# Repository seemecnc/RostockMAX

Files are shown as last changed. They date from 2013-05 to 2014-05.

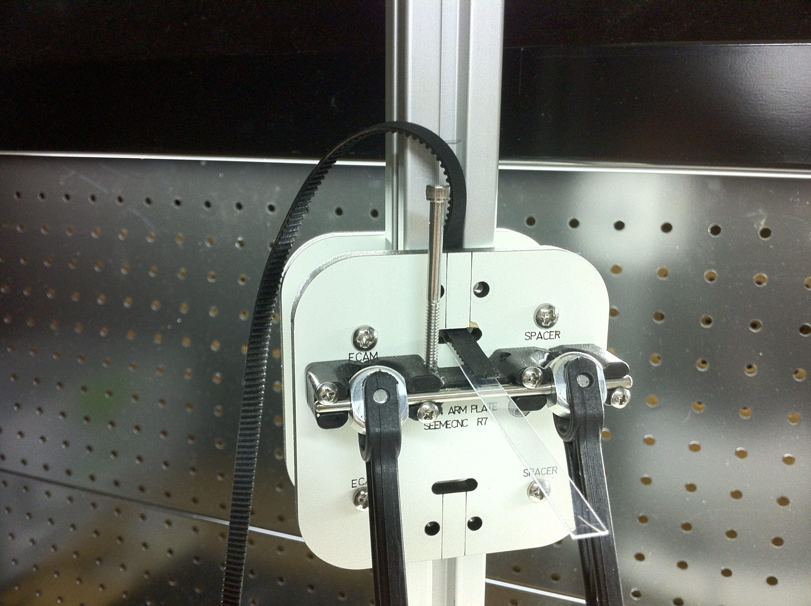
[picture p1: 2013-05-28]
ASSEMBLY_MANUAL/belt-routing-trick.jpg

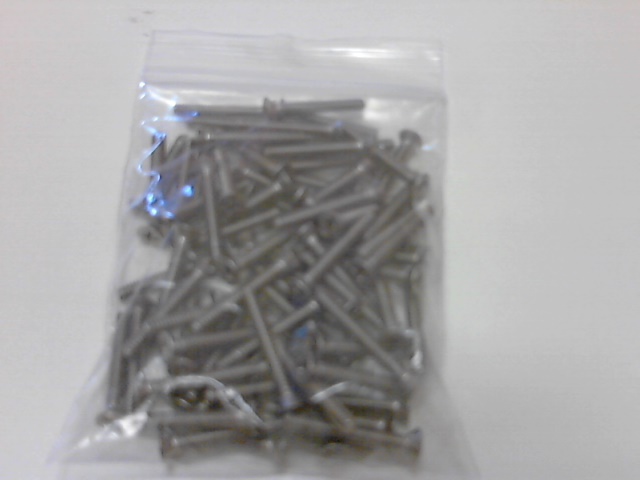
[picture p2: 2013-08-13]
PACKING_LIST/img/Picture 91.jpg

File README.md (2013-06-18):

RostockMAX
==========
Author:  SeeMeCNC
Initially created here on github 5/28/2013, origionally hosted on reprap.org
Source files for the Rostock MAX Delta 3D Printer by SeeMeCNC

Use the CAD_FILES folder to obtain the source cad files such as the dxf's for lasercut parts, .stl and .iges 
files for other parts.   

For the assembly manual, use the folder ASSEMBLY_MANUAL

Note that github has problems with large files.  If you get the error, "Error: blob is too big" when
trying to view the PDF file, you can obtain it here: 
http://www.geneb.org/rostock-max/Rostock-MAX-Assembly-Guide.pdf

For firmware, use the repo http://github.com/seemecnc/RepetierMAX

For the new EZStruder, which started shipping with all kits around 5/20/13, please see
https://github.com/seemecnc/EZStruder

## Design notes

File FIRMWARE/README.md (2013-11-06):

# Repetier-Firmware - the fast and user friendly firmware

##########  Modified by SeeMeCNC for use with the Rostock MAX kits ###########
This firmware has changes made specific to the Rostock MAX.  Mainly, calibartion settings etc... as well as
some functionalities for the RAMBo board by ultimachine.

PLEASE CHECK THE CONFIGURATION.H FILE BEFORE UPLOADING
Check the steps per mm settings, pulley tooth count etc... to make sure they correspond with 
your machine's settings

For questions regarding changes, email johnoly (john@seemecnc.com)

by repetier  (repetierdev@gmail.com)

For documentation please visit [http://www.repetier.com/documentation/repetier-firmware/](http://www.repetier.com/documentation/repetier-firmware/)

Beta version with added delta move and homing calculations and several other features for delta printers.

To set rod height on a delta printer use command M251 which will allow you to measure 
the rod length or, if you have an LCD panel then you can select delta calibration in the
configuration menu.

Version 0.81  03.02.2013

## Introduction

Repetier-Firmware is a firmware for RepRap like 3d-printer powered with
an arduino compatible controller.
This firmware is a nearly complete rewrite of the sprinter firmware by kliment
which based on Tonokip RepRap firmware rewrite based off of Hydra-mmm firmware.
Some ideas were also taken from Teacup, Grbl and Marlin.

Supported boards:

The following boards are supported by setting the proper motherboard type.Other boards
require a matching pin definition.

* MEGA/RAMPS up to 1.2       = 3
* RAMPS 1.3/RAMPS 1.4        = 33
* Gen6                       = 5 
* Gen6 deluxe                = 51
* Sanguinololu up to 1.1     = 6
* Sanguinololu 1.2 and above = 62
* Gen7 1.1 till 1.3.x        = 7
* Gen7 1.4.1 and later       = 71
* Teensylu (at90usb)         = 8 // requires Teensyduino
* Printrboard (at90usb)      = 9 // requires Teensyduino
* Foltyn 3D Master           = 12
* MegaTronics                = 70
* RUMBA                      = 80  // Get it from reprapdiscount
* Rambo                      = 301

## Features

- RAMP acceleration support.
- Path planning for higher print speeds.
- Trajectory smoothing for smoother lines.
- Ooze prevention system for faster anti ooze then slicer can do,
- Nozzle pressure control for improved print quality with RAMPS.
- Fast - 40000 Hz and more stepper frequency is possible with a 16 MHz AVR. 
- Multiple extruder supported (max. 6 extruder).
- Standard ASCII and improved binary (Repetier protocol) communication.
- Autodetect the command protocol, so it will work with any host software.
- Continuous monitoring of one temperature.
- Important parameters are stored in EEPROM and can easily be modified without
  recompilation of the firmware.
- Stepper control is handled in an interrupt routine, leaving time for
  filling caches for next move.
- PID control for extruder/heated bed temperature.
- Interrupt based sending buffer (Arduino library normally waits for the
  recipient to receive written data)
- Small RAM memory print, resulting in large caches.
- Supports SD-cards.
- mm and inches can be used for G0/G1
- Arc support
- Works with Skeinforge 41, all unknown commands are ignored.
- Dry run : Execute yout GCode without using the extruder. This way you can
  test for non-extruder related failures without actually printing.

## Controlling firmware

Also you can control the firmware with any reprap compatible host, you will only get
the full benefits with the following products, which have special code for this
firmware:

* [Repetier-Host for Windos/Linux](http://www.repetier.com/download/)
* [Repetier-Host for Mac](http://www.repetier.com/download/)
* [Repetier-Server](http://www.repetier.com/repetier-server-download/)

## Installation

For documentation and installation please visit 
[http://www.repetier.com/documentation/repetier-firmware/](http://www.repetier.com/documentation/repetier-firmware/).

## Changelog

See changelog.txt

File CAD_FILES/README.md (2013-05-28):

RostockMAX CAD source files
==========

Source files for the Rostock MAX Delta 3D Printer by SeeMeCNC
These files are distibuted GPL, feel free to enjoy, but give credit where due.

The DXFs folder contains the 4 lasercut sheets needed to cut the parts for a Rostock MAX.

Sheets 1 thru 3 are 18" x 32" x .270" thick melamine laminate, and the files have been optimized for
that material.  It also works with 1/4" acrylic, however the tabs are slightly oversized for 1/4" material.

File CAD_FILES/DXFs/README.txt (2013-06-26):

Rostock MAX dxf files of laser cut parts

The newest files are WOOD RMAX EZ SHEET x OF 3.dxf

These files are what are shipping as of 6/15, the older SHEETx.dxf files have
the old style side mounted extruder mounts etc...

26Jun13 gwb Added "RMAX EXTRUDER MOUNTING KIT.DXF" - this is just the parts needed to
            make the new top mounted extruder and spool mount.

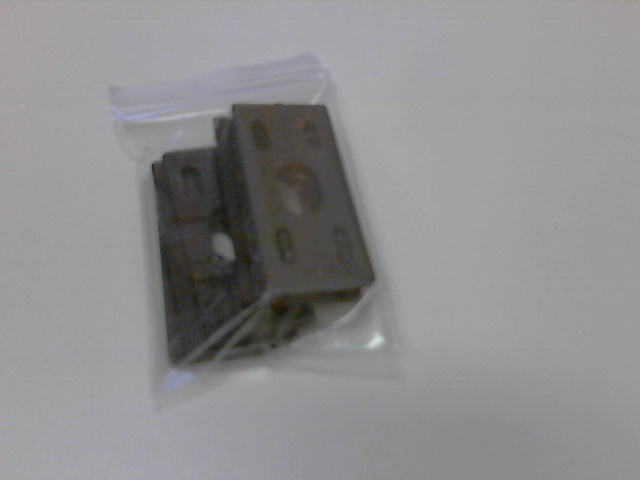
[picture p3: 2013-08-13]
PACKING_LIST/img/Picture 102.jpg

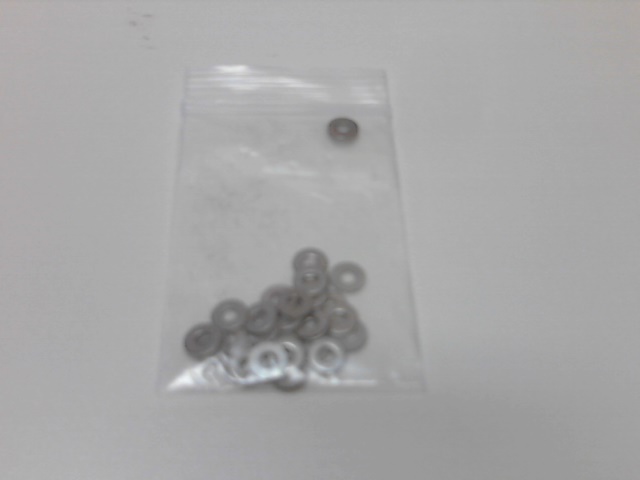
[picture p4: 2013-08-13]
PACKING_LIST/img/Picture 79.jpg

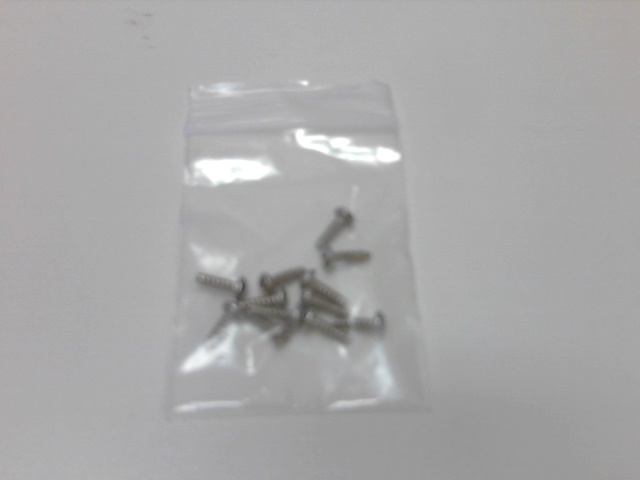
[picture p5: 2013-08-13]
PACKING_LIST/img/Picture 81.jpg

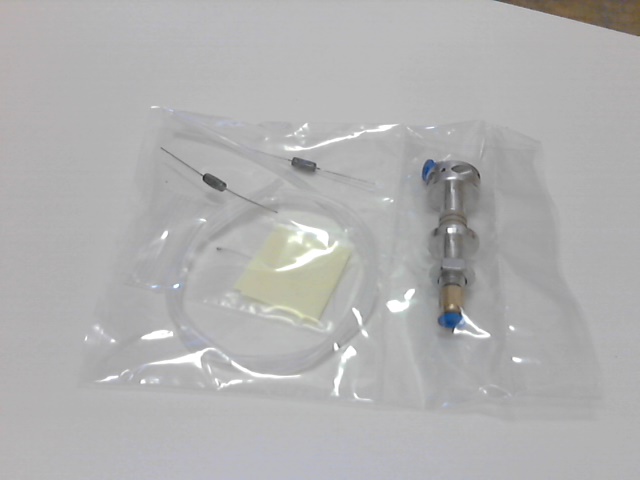
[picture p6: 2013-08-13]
PACKING_LIST/img/Picture 122.jpg

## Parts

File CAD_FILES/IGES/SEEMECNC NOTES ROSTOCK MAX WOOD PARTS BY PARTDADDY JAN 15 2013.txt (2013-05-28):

by PartDaddy
Jan 25, 2013

To our peers in the open source community...

Here's the Rostock MAX IGES files so many of you requested. Yes, I know how hard it is to 
reverse engineer STL files. 

These IGES files should work for just about any CAD software. If they do not,
email us and I will fixt them.

~Steve Wygant aka PartDaddy

SeeMeCNC

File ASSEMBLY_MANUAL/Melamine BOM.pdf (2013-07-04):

Sheet1

Part # | Qty | Description
68324 | 1 Hot End Spacer
68328 | 1 Hot End Adapter
68343 | 3 Carriage Plate
68344 | 3 Arm Plate
68345 | 2 Spool Axle
68351 | 1 Table
68352 | 3 | Tri Support
68355 | 1 Base
68356 | 1 Power Supply Retainer
68357 | 1 Support Panel
68358 | 1 Door
68361 | 7 Cover Bracket
68364 | 3 Motor Mount
68368 | 1 Top Support Plate
68369 | 6 Idler Mount
68370 | 3 Top Clamp
68377 | 3 T Slot Support
68381 | 6 Axle Support
68387 | 2 | Extruder Bracket
68388 | 3 | Spacer Extruder Support
68389 | 1 | Extruder Clamp
68392 | 2 Bracket For Filament Spool
68410 | 1 LCD Face
68411 | 2 Stand Off LCD
70769 | 3 | Spacer (top mounted extruder)
70770 | 1 | Brace (top mounted extruder)
70771 | 1 Part A (Spool holder)
70772 | 1 Part B (Spool holder)
70773 | 2 Arm (Spool holder)
70774 | 1 Part C (Spool holder)
70777 | 1 | Motor Support (top mounted extruder)
70778 | 1 | EZStruder Adapter Hanger
70779 | 1 | EZStruder Adapter
N/A | 2 Door Keeper
Total | 72

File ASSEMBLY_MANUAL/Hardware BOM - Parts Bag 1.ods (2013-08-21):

Part # | Qty | Description
Parts Bag #1
30650 | 6 | 2-56 Pan head screws
30642 | 6 | 2-56 Hex nuts
30006 | 6 | 6-32x5/8” Socket Head Cap Screw
30037 | 22 | 6-32x2” Pan head screws
30034 | 10 | 6-32x1.75” Pan head screw
32005 | 25 | ¼-20 T-Slot Nut
30419 | 25 | ¼-20 Button Head Cap Screw
29998 | 6 | 10x32x5/8” Nylon Pan Head Screw
30170 | 6 | Nylon Hex Nut
44010 | 6 | Rubber Foot
17505 | 6 | Leg for #44010 Rubber Foot
30449 | 26 | #4 Flat Washer
30251 | 12 | #4x1/4” Pan Head Sheet Metal Screw
30250 | 12 | #4x3/8” Pan Head Sheet Metal Screw
30222 | 27 | 4-40 T-Nut
30238 | 4 | 4-40x1-1/4” Pan Head Screw
30236 | 16 | 4-40x3/4” Flat Head Screw
30232 | 12 | 4-40x1/2” Socket Head Cap Screw
30318 | 12 | M3x.5 Pan Head Screw
30121 | 4 | 6-32x1/2” Nylon Pan Head Screw
30450 | 50 | #6 Flat Washer
35065 | 24 | 608ZZ Ball Bearing
30164 | 114 | 6-32 Nylon Lock Nut
30132 | 78 | 6-32x1” Flat Head Screw

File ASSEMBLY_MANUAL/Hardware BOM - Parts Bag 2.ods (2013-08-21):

Part # | Qty | Description
Parts Bag #2
68309 | 12 | Universal Joint
68326 | 18 | Cheapskate Carriage Bearing Spacer
68340 | 18 | Cheapskate Idler Bearing Spacer
68334 | 3 | Hot End Platform Spacer (Aluminum)
63825 | 6 | U-Joint Axles
68315 | 12 | Cheapskate Eccentric Carriage Tensioner

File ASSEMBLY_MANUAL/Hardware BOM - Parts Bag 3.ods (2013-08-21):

Part # | Qty | Description
Parts Bag #3
71505 | 20 | Plastic Spacers
71622 | 6 | Belt Clamps
68332 | 3 | Carriage Base
68304 | 2 | Platform Halves
58761 | 6 | Binder Clips
26159 | 1 | Toggle Switch
26164 | 15 | Wire Ties
39835 | 1 | 20 Tooth GT2 Timing Pulley Kit
 |  | 3 Pulleys, 6 Set Screws, 1 Allen Wrench
68303 | 6 | Rostock MAX Molded Arms

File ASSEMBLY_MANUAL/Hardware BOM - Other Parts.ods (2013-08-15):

Part # | Qty | Description
Onyx Bed Pack
70505 | 6 | Plastic Spacers
30236 | 6 | 4-40x3/4” Flat Head Screw
30222 | 6 | 4-40 T-Nut
 | 1 | 100K Thermistor
 | 1 | Red LED
 | 1 | 4.7K Resistor
58742 | 1 | 300MM Onyx Round Heated Bed
 | 1 | Onyx Laser Cut Insulator
Electronics
 | 1 | RAMBo Electronics Package
 |  | (Incl. Board, end stop wiring and thermistor wires)
26720 | 1 | RRD LCD Controller with SD card and RAMBo
 |  | LCD Adapter
 | 1 | USB Cable
26501 | 4 | NEMA 17 Stepper Motor
26309 | 1 | 25MMx25MMx10MM 12v Fan
 | 1 | ATX Power Supply
Miscellaneous
26602 | 1 | 300MM Borosilicate Glass Build Plate
 |  | Included in kits purchased after 8/11/2013
 | 3 | 32” Aluminum Extrusions
Belt Pack
 | 3 | 75” GT2 2MM Pitch Belts
68336 | 30 | Bearing Covers
Hot End Pack
 | 2 | 6.8 Ohm Heating Resistors
 | 1 | 100k Thermistor
 | 1 | 24”x2MM ID x 4MM OD PTFE Tubing
 | 2 | 4MM PTC Fitting
 | 1 | Assembled Hot End
 | 1 | 2” PTFE sleeve for thermistor wires

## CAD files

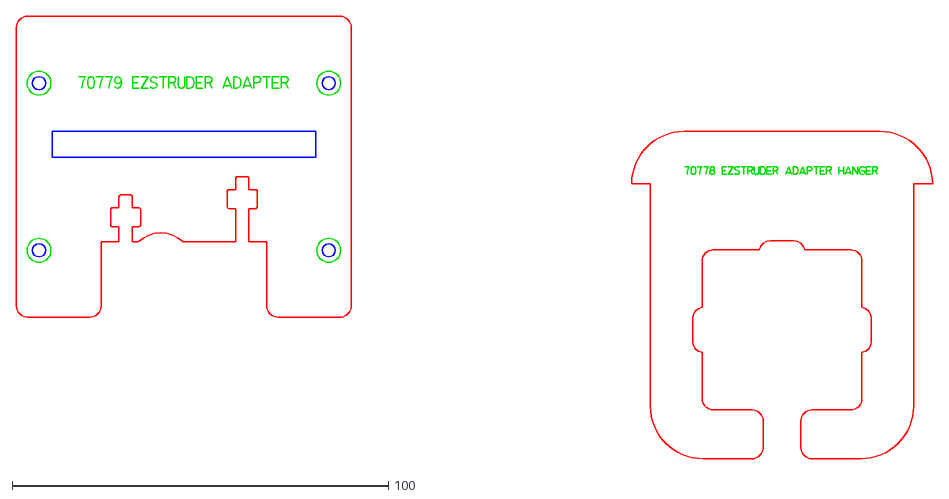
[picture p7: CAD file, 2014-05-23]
CAD_FILES/DXFs/EZSTRUDER_HANGER_ADAPTER.DXF
243.5 x 117.6

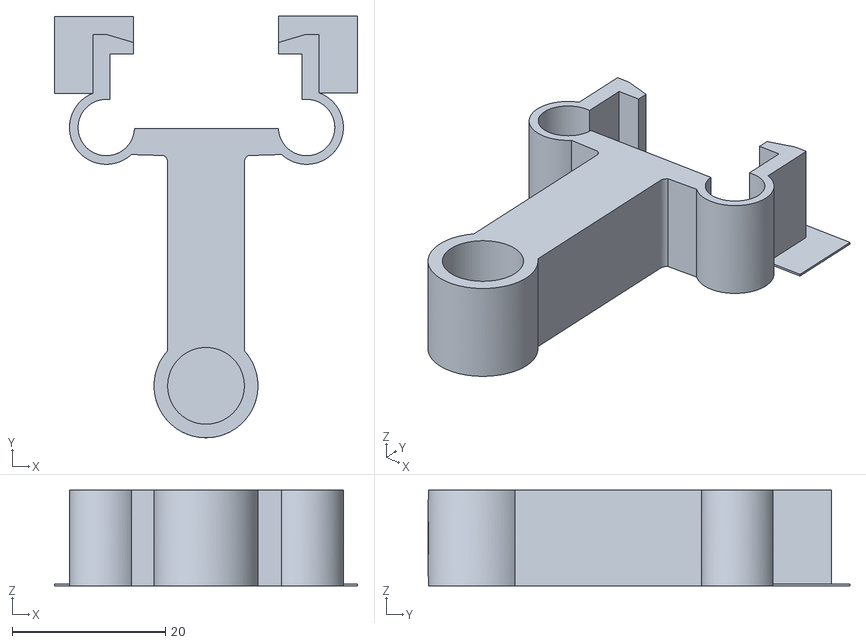
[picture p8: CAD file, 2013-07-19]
PRINTED_ADDONS/wire guide post mounting clip.stl
39.5 x 55.0 x 12.5

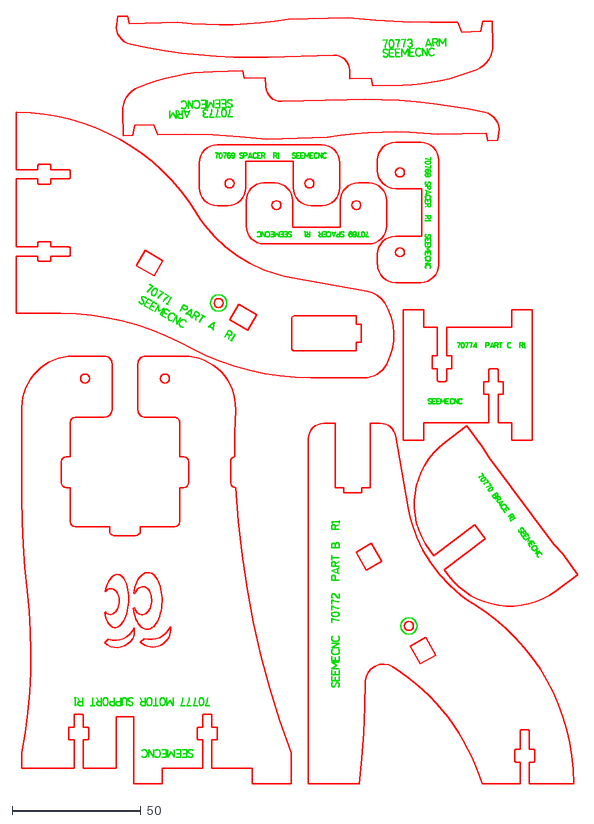
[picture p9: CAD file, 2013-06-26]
CAD_FILES/DXFs/RMAX EXTRUDER MOUNTING KIT.dxf
218.1 x 298.1

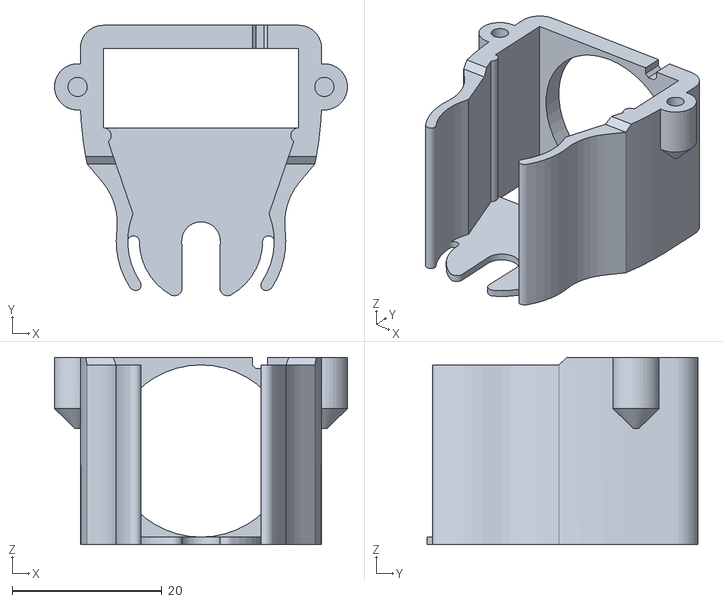
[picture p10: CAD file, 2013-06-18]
PRINTED_ADDONS/S3_Beta_Fanshroud.stl
39.1 x 36.1 x 25.0

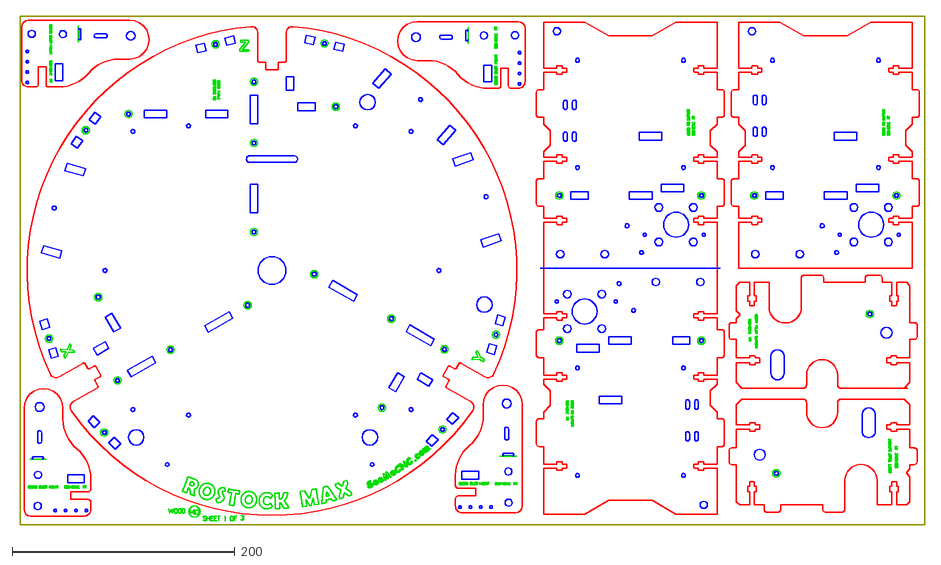
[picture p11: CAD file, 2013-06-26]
CAD_FILES/DXFs/WOOD RMAX EZ SHEET 1 OF 3.DXF
816.2 x 457.2

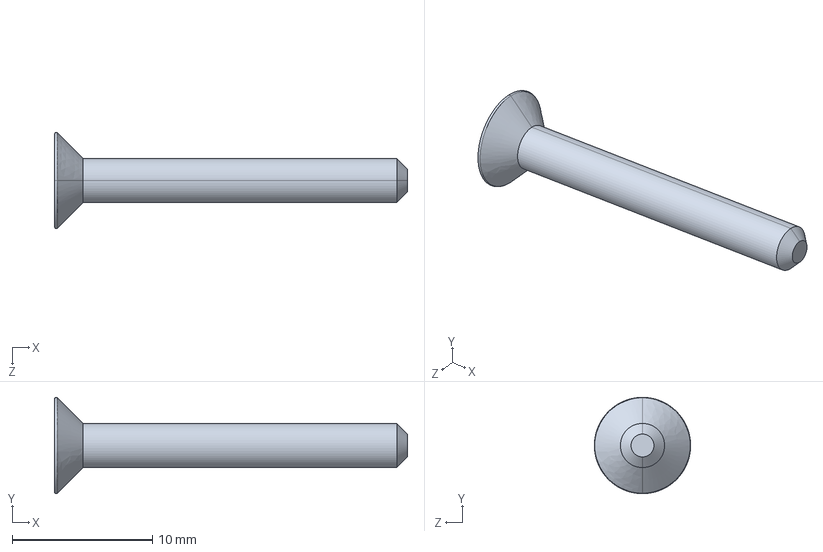
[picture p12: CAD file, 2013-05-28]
CAD_FILES/IGES/6-32 X 1 PHILLIP FLAT HEAD.IGS
25.1 x 6.86 x 6.86 mm

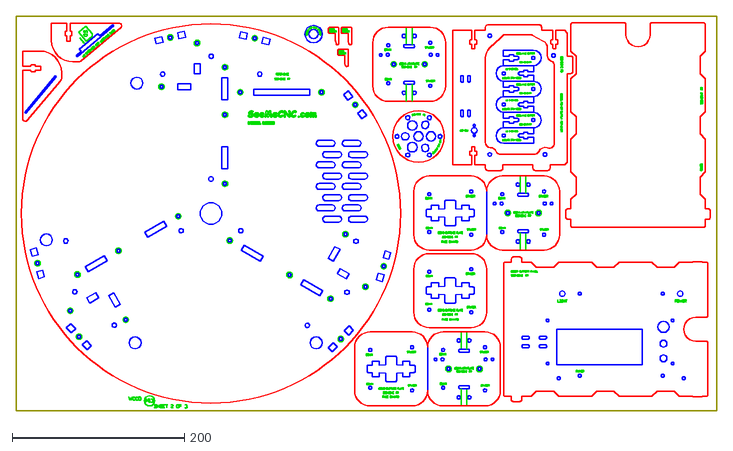
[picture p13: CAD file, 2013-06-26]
CAD_FILES/DXFs/WOOD RMAX EZ SHEET 2 OF 3.DXF
812.8 x 457.2

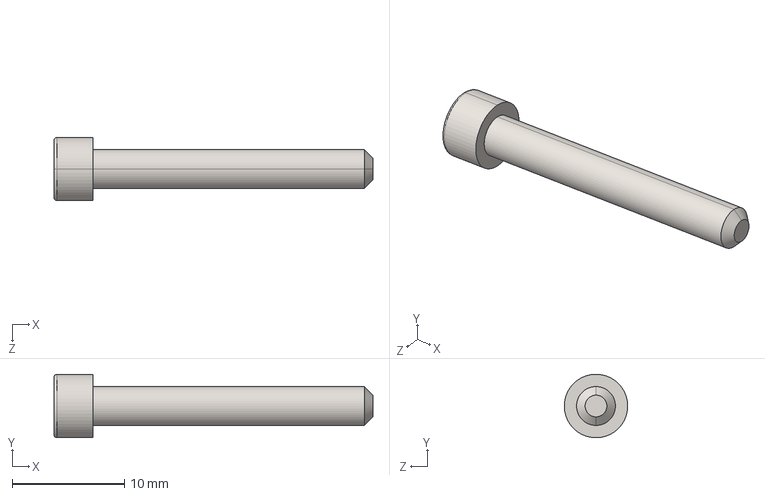
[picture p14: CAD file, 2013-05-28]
CAD_FILES/IGES/6-32 x 1000L SHCS.IGS
28.4 x 5.64 x 5.64 mm

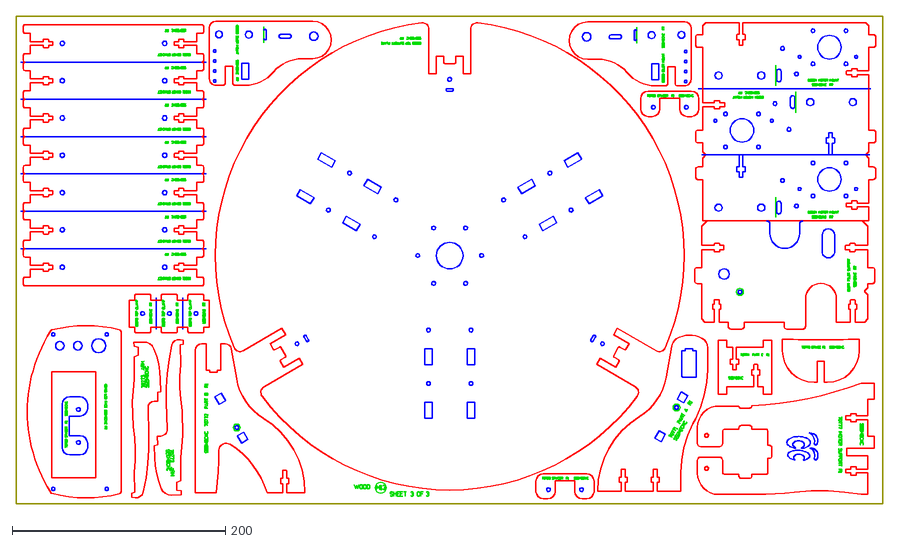
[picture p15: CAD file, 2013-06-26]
CAD_FILES/DXFs/WOOD RMAX EZ SHEET 3 OF 3.DXF
812.8 x 457.2

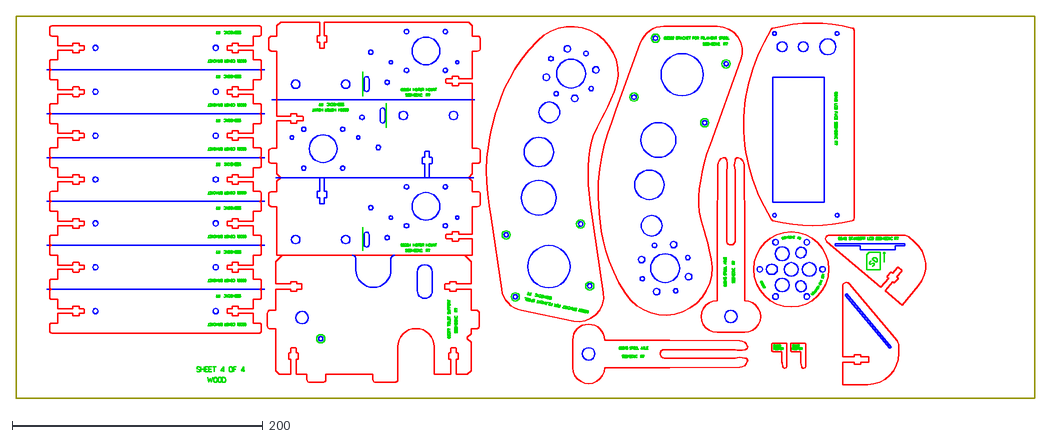
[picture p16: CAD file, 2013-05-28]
CAD_FILES/DXFs/SHEET4.DXF
812.8 x 304.8

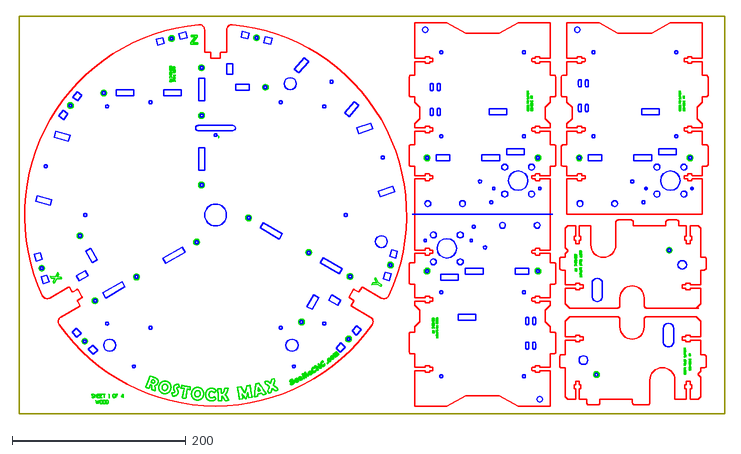
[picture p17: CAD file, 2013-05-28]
CAD_FILES/DXFs/SHEET1.DXF
816.2 x 457.2

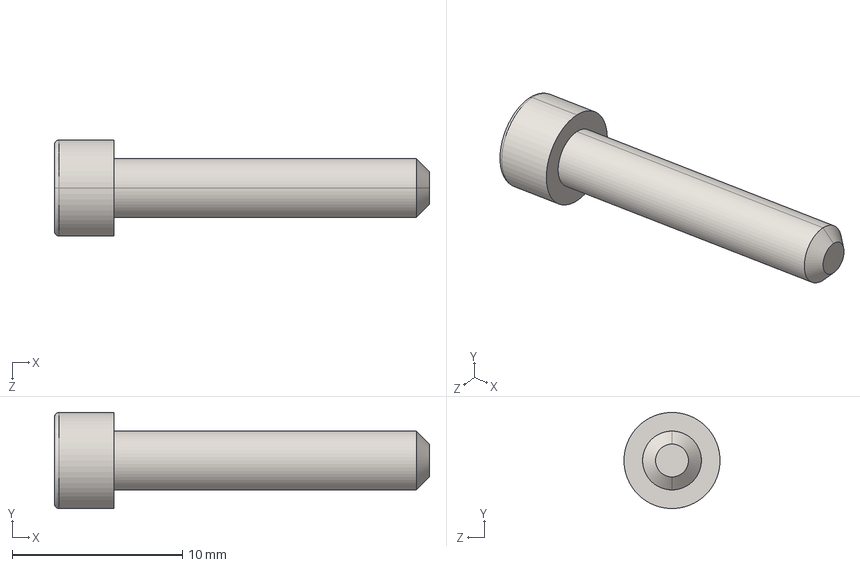
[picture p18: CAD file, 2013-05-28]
CAD_FILES/IGES/6-32 x 0750L SHCS.IGS
22.0 x 5.64 x 5.64 mm

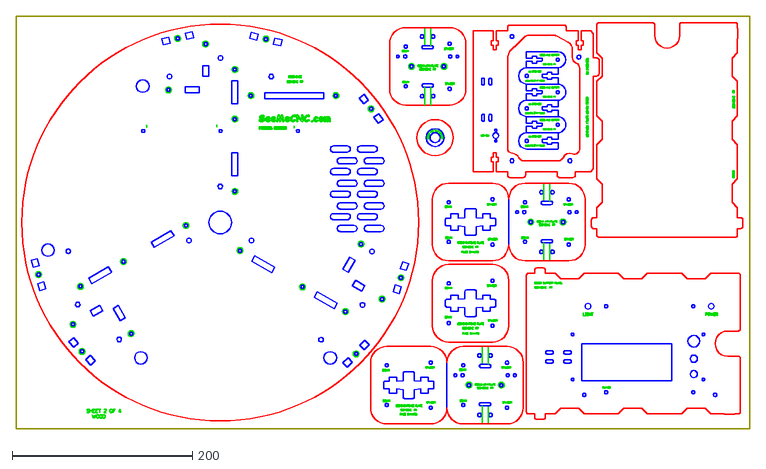
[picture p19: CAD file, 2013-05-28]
CAD_FILES/DXFs/SHEET2.DXF
812.8 x 457.2

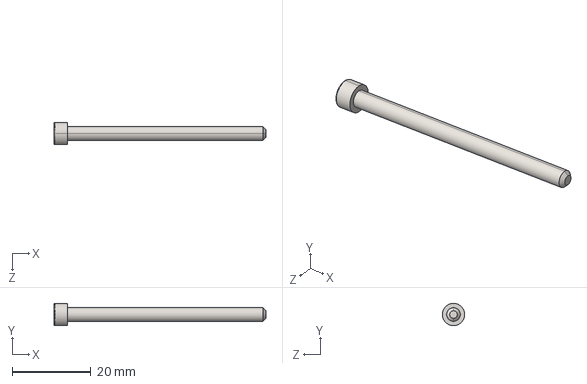
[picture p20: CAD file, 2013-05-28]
CAD_FILES/IGES/6-32 x 2000L SHCS.IGS
53.8 x 5.64 x 5.64 mm

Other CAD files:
CAD_FILES/IGES/608-bearing.IGS
CAD_FILES/IGES/No 4 x 0500L PANHSheet Metal.IGS
CAD_FILES/IGES/SEEMECNC BELT CLAMP FOLDED.IGS
CAD_FILES/IGES/No 4 x 0250L PANH Sheet Metal.IGS
CAD_FILES/IGES/0250-20 T-slot Nut.IGS
CAD_FILES/IGES/0250-20 x 0500L Button Head Cap Screw.IGS
CAD_FILES/IGES/10-32 x 0625L Pan Head Screw Natural Nylon.IGS
CAD_FILES/IGES/4-40 x 0500 SHCS.IGS
CAD_FILES/IGES/4-40 x 0750 SHCS.IGS
CAD_FILES/IGES/58742 R2 ONYX.IGS
CAD_FILES/IGES/6-32 x 0500L PH Screw Nylon.IGS
CAD_FILES/IGES/6-32 x 1750L SHCS.IGS
CAD_FILES/IGES/68303 Rod.IGS
CAD_FILES/IGES/68304 platform.IGS
CAD_FILES/IGES/68309 Universal Joint.IGS
CAD_FILES/IGES/68310 1X1 TSLOT PROFILE.IGS
CAD_FILES/IGES/68315 Eccentric Spacer.IGS
CAD_FILES/IGES/68316 Bowden Hot End PTC adapter.IGS
CAD_FILES/IGES/68324 Hot End Spacer.IGS
CAD_FILES/IGES/68325 U Shaft Axle.IGS
CAD_FILES/IGES/68326 Bushing 3mm.IGS
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

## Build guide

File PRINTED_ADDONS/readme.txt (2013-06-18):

the 70766 fan shroud is for the SeeMeCNC Hot End and a Rostock MAX.  
Made to use a 25mm x25mm x 10mm fan 
Mounts to Rostock/RostockMAX Platform

the S3 Beta fanshroud is for the S3 All Metal BETA Hotend testing.  This HotEnd only 
seems to work with ABS, Nylon, HIPS, but not PLA well yet  :(

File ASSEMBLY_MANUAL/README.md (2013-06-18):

RostockMAX Assembly/User Manual
==========

This manual is written/maintained by user:Geneb

The manual is "feature complete" as of 18Jun13.  One additional chapter "Upgrades"
will be added soon.
-gwb

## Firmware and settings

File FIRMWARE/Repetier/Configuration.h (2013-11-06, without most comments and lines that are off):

#define CONFIGURATION_H
#define NUM_EXTRUDER 1
#define MOTHERBOARD 301
#include "pins.h"
#define DRIVE_SYSTEM 3
#if DRIVE_SYSTEM==3
    #define DELTA_DRIVE_TYPE 0
    #if DELTA_DRIVE_TYPE == 0
      #define BELT_PITCH 2
      #define PULLEY_TEETH 20
      #define PULLEY_CIRCUMFERENCE (BELT_PITCH * PULLEY_TEETH)
    #elif DELTA_DRIVE_TYPE == 1
      #define PULLEY_DIAMETER 10
      #define PULLEY_CIRCUMFERENCE (PULLEY_DIAMETER * 3.1415927)
    #endif
    #define STEPS_PER_ROTATION 200
    #define MICRO_STEPS 16
    #define MAX_DELTA_SEGMENTS_PER_LINE 30
    #define AXIS_STEPS_PER_MM ((float)(MICRO_STEPS * STEPS_PER_ROTATION) / PULLEY_CIRCUMFERENCE)
    #define XAXIS_STEPS_PER_MM AXIS_STEPS_PER_MM
    #define YAXIS_STEPS_PER_MM AXIS_STEPS_PER_MM
    #define ZAXIS_STEPS_PER_MM AXIS_STEPS_PER_MM
#else
    #define XAXIS_STEPS_PER_MM 80.000
    #define YAXIS_STEPS_PER_MM 80.000
    #define ZAXIS_STEPS_PER_MM 80.000
#endif
#define EXTRUDER_FAN_COOL_TEMP 40
#define EXT0_X_OFFSET 0
#define EXT0_Y_OFFSET 0
#define EXT0_STEPS_PER_MM 92.000 //steves extruder    set to 92 for ezstruder
#define EXT0_TEMPSENSOR_TYPE 8
#define EXT0_TEMPSENSOR_PIN TEMP_0_PIN
#define EXT0_HEATER_PIN HEATER_0_PIN
#define EXT0_STEP_PIN E0_STEP_PIN
#define EXT0_DIR_PIN E0_DIR_PIN
#define EXT0_INVERSE true
#define EXT0_ENABLE_PIN E0_ENABLE_PIN
#define EXT0_ENABLE_ON false
#define EXT0_MAX_FEEDRATE 40
#define EXT0_MAX_START_FEEDRATE 10
#define EXT0_MAX_ACCELERATION 3500
#define EXT0_HEAT_MANAGER 1
#define EXT0_WATCHPERIOD 1
#define EXT0_PID_INTEGRAL_DRIVE_MAX 205
#define EXT0_PID_INTEGRAL_DRIVE_MIN 60
#define EXT0_PID_P   11.63
#define EXT0_PID_I   0.43
#define EXT0_PID_D 78.65
#define EXT0_PID_MAX 255
#define EXT0_ADVANCE_K 0.0f
#define EXT0_ADVANCE_L 0.0f
#define EXT0_WAIT_RETRACT_TEMP 		150
#define EXT0_WAIT_RETRACT_UNITS 	0
#define EXT0_SELECT_COMMANDS "M120 S5 P5\nM117 Extruder 1"
#define EXT0_DESELECT_COMMANDS ""
#define EXT0_EXTRUDER_COOLER_PIN 7
#define EXT0_EXTRUDER_COOLER_SPEED 255
#define EXT1_X_OFFSET 10
#define EXT1_Y_OFFSET 0
#define EXT1_STEPS_PER_MM 373
#define EXT1_TEMPSENSOR_TYPE 3
#define EXT1_TEMPSENSOR_PIN TEMP_2_PIN
#define EXT1_HEATER_PIN HEATER_2_PIN
#define EXT1_STEP_PIN E1_STEP_PIN
#define EXT1_DIR_PIN E1_DIR_PIN
#define EXT1_INVERSE false
#define EXT1_ENABLE_PIN E1_ENABLE_PIN
#define EXT1_ENABLE_ON false
#define EXT1_MAX_FEEDRATE 25
#define EXT1_MAX_START_FEEDRATE 12
#define EXT1_MAX_ACCELERATION 10000
#define EXT1_HEAT_MANAGER 1
#define EXT1_WATCHPERIOD 1
#define EXT1_PID_INTEGRAL_DRIVE_MAX 130
#define EXT1_PID_INTEGRAL_DRIVE_MIN 60
#define EXT1_PID_P   24
#define EXT1_PID_I   0.88
#define EXT1_PID_D 200
#define EXT1_PID_MAX 255
#define EXT1_ADVANCE_K 0.0f
#define EXT1_ADVANCE_L 0.0f
#define EXT1_WAIT_RETRACT_TEMP 	150
#define EXT1_WAIT_RETRACT_UNITS	40
#define EXT1_SELECT_COMMANDS "M120 S5 P15\nM117 Extruder 2"
#define EXT1_DESELECT_COMMANDS ""
#define EXT1_EXTRUDER_COOLER_PIN -1
#define EXT1_EXTRUDER_COOLER_SPEED 255
#define RETRACT_DURING_HEATUP true
#define PID_CONTROL_RANGE 15
#define SKIP_M109_IF_WITHIN 2
#define SCALE_PID_TO_MAX 0
#define NUM_TEMPS_USERTHERMISTOR0 28
#define USER_THERMISTORTABLE0  {\
  {1*4,864*8},{21*4,300*8},{25*4,290*8},{29*4,280*8},{33*4,270*8},{39*4,260*8},{46*4,250*8},{54*4,240*8},{64*4,230*8},{75*4,220*8},\
  {90*4,210*8},{107*4,200*8},{128*4,190*8},{154*4,180*8},{184*4,170*8},{221*4,160*8},{265*4,150*8},{316*4,140*8},{375*4,130*8},\
  {441*4,120*8},{513*4,110*8},{588*4,100*8},{734*4,80*8},{856*4,60*8},{938*4,40*8},{986*4,20*8},{1008*4,0*8},{1018*4,-20*8}	}
#define NUM_TEMPS_USERTHERMISTOR1 0
#define USER_THERMISTORTABLE1  {}
#define NUM_TEMPS_USERTHERMISTOR2 0
#define USER_THERMISTORTABLE2  {}
#define GENERIC_THERM1_R0 100000
#define GENERIC_THERM1_T0 25
#define GENERIC_THERM1_BETA 4450
#define GENERIC_THERM1_MIN_TEMP -20
#define GENERIC_THERM1_MAX_TEMP 300
#define GENERIC_THERM1_R1 0
#define GENERIC_THERM1_R2 4700
#define GENERIC_THERM2_R0 1042.7
#define GENERIC_THERM2_T0 170
#define GENERIC_THERM2_BETA 4036
#define GENERIC_THERM2_MIN_TEMP -20
#define GENERIC_THERM2_MAX_TEMP 300
#define GENERIC_THERM2_R1 0
#define GENERIC_THERM2_R2 4700
#define GENERIC_THERM3_R0 1042.7
#define GENERIC_THERM3_T0 170
#define GENERIC_THERM3_BETA 4036
#define GENERIC_THERM3_MIN_TEMP -20
#define GENERIC_THERM3_MAX_TEMP 300
#define GENERIC_THERM3_R1 0
#define GENERIC_THERM3_R2 4700
#define GENERIC_THERM_VREF 5
#define GENERIC_THERM_NUM_ENTRIES 28
#define HAVE_HEATED_BED true
#define HEATED_BED_MAX_TEMP 115
#define SKIP_M190_IF_WITHIN 5
#define HEATED_BED_SENSOR_TYPE 8
#define HEATED_BED_SENSOR_PIN TEMP_BED_PIN  //CHANGE FROM TEMP_1_PIN TO TEMP_BED_PIN FOR RAMBo
#define HEATED_BED_HEATER_PIN HEATER_BED_PIN   //CHANGE FROM HEATER_1_PIN TO TEMP_BED_PIN FOR RAMBo
#define HEATED_BED_SET_INTERVAL 5000
#define HEATED_BED_HEAT_MANAGER 1
#define HEATED_BED_PID_INTEGRAL_DRIVE_MAX 255
#define HEATED_BED_PID_INTEGRAL_DRIVE_MIN 80
#define HEATED_BED_PID_PGAIN   15.0
#define HEATED_BED_PID_IGAIN   0.9
#define HEATED_BED_PID_DGAIN 40.0
#define HEATED_BED_PID_MAX 230
#define TEMP_PID true
#define MINTEMP 5
#define MAXTEMP 250
#define MIN_DEFECT_TEMPERATURE -10
#define MAX_DEFECT_TEMPERATURE 300
#define ANALOG_REF ANALOG_REF_AVCC
#define ENDSTOP_PULLUP_X_MIN true
#define ENDSTOP_PULLUP_Y_MIN true
#define ENDSTOP_PULLUP_Z_MIN true
#define ENDSTOP_PULLUP_X_MAX true
#define ENDSTOP_PULLUP_Y_MAX true
#define ENDSTOP_PULLUP_Z_MAX true
#define ENDSTOP_X_MIN_INVERTING true
#define ENDSTOP_Y_MIN_INVERTING true
#define ENDSTOP_Z_MIN_INVERTING true
#define ENDSTOP_X_MAX_INVERTING false
#define ENDSTOP_Y_MAX_INVERTING false
#define ENDSTOP_Z_MAX_INVERTING false
#define MIN_HARDWARE_ENDSTOP_X false
#define MIN_HARDWARE_ENDSTOP_Y false
#define MIN_HARDWARE_ENDSTOP_Z false
#define MAX_HARDWARE_ENDSTOP_X true
#define MAX_HARDWARE_ENDSTOP_Y true
#define MAX_HARDWARE_ENDSTOP_Z true
#define X_ENABLE_ON 0
#define Y_ENABLE_ON 0
#define Z_ENABLE_ON 0
#define DISABLE_X false
#define DISABLE_Y false
#define DISABLE_Z false
#define DISABLE_E false
#define INVERT_X_DIR true
#define INVERT_Y_DIR true
#define INVERT_Z_DIR true
#define X_HOME_DIR 1
#define Y_HOME_DIR 1
#define Z_HOME_DIR 1
#define max_software_endstop_r true
#define min_software_endstop_x false
#define min_software_endstop_y false
#define min_software_endstop_z false
#define max_software_endstop_x true
#define max_software_endstop_y true
#define max_software_endstop_z true
#define ENDSTOP_X_BACK_MOVE 10
#define ENDSTOP_Y_BACK_MOVE 10
#define ENDSTOP_Z_BACK_MOVE 10
#define ENDSTOP_X_RETEST_REDUCTION_FACTOR 4
#define ENDSTOP_Y_RETEST_REDUCTION_FACTOR 4
#define ENDSTOP_Z_RETEST_REDUCTION_FACTOR 4
#define ENDSTOP_X_BACK_ON_HOME 5
#define ENDSTOP_Y_BACK_ON_HOME 5
#define ENDSTOP_Z_BACK_ON_HOME 5
#define ALWAYS_CHECK_ENDSTOPS true
#define X_MAX_LENGTH 360.8
#define Y_MAX_LENGTH 360.8
#define Z_MAX_LENGTH 360.8
#define X_MIN_POS 0
#define Y_MIN_POS 0
#define Z_MIN_POS 0
#define MICROSTEP_MODES {16,16,16,16,16} // [1,2,4,8,16]
#define MOTOR_CURRENT {175,175,175,225,0} // Values 0-255 (RAMBO 135 = ~0.75A, 185 = ~1A)
#if DRIVE_SYSTEM==3
#define DELTA_DIAGONAL_ROD 269.0 // mm
#define DELTA_SEGMENTS_PER_SECOND_PRINT 200 // Move accurate setting for print moves
#define DELTA_SEGMENTS_PER_SECOND_MOVE 70 // Less accurate setting for other moves
#define END_EFFECTOR_HORIZONTAL_OFFSET 33
#define CARRIAGE_HORIZONTAL_OFFSET 35
#define PRINTER_RADIUS 198.25
#define DELTA_RADIUS (PRINTER_RADIUS-END_EFFECTOR_HORIZONTAL_OFFSET-CARRIAGE_HORIZONTAL_OFFSET)
#define STEP_COUNTER
#define SOFTWARE_LEVELING
#endif
#define STEPPER_INACTIVE_TIME 6000
#define MAX_INACTIVE_TIME 9000
#define MAX_FEEDRATE_X 200
#define MAX_FEEDRATE_Y 200
#define MAX_FEEDRATE_Z 200
#define HOMING_FEEDRATE_X 80
#define HOMING_FEEDRATE_Y 80
#define HOMING_FEEDRATE_Z 80
#define ENABLE_BACKLASH_COMPENSATION false
#define Z_BACKLASH 0
#define X_BACKLASH 0
#define Y_BACKLASH 0
#define RAMP_ACCELERATION 1
#define STEPPER_HIGH_DELAY 0
#define STEP_DOUBLER_FREQUENCY 12000
#define ALLOW_QUADSTEPPING true
#define DOUBLE_STEP_DELAY 1 // time in us
#define MAX_HALFSTEP_INTERVAL 1999
#define MAX_ACCELERATION_UNITS_PER_SQ_SECOND_X 3500
#define MAX_ACCELERATION_UNITS_PER_SQ_SECOND_Y 3500
#define MAX_ACCELERATION_UNITS_PER_SQ_SECOND_Z 3500
#define MAX_TRAVEL_ACCELERATION_UNITS_PER_SQ_SECOND_X 3500
#define MAX_TRAVEL_ACCELERATION_UNITS_PER_SQ_SECOND_Y 3500
#define MAX_TRAVEL_ACCELERATION_UNITS_PER_SQ_SECOND_Z 3500
#define MAX_JERK 20.0
#define MAX_ZJERK 20.0
#define MOVE_CACHE_SIZE 16
#define MOVE_CACHE_LOW 10
#define LOW_TICKS_PER_MOVE 250000
#define TIMER0_PRESCALE 64
#define MIN_EXTRUDER_TEMP 0
#define USE_OPS 1
#define OPS_MODE 0
#define OPS_MIN_DISTANCE 0.8
#define OPS_MOVE_AFTER 50.0
#define OPS_RETRACT_DISTANCE 1.5
#define OPS_RETRACT_BACKLASH 0.0
#define USE_ADVANCE
#define BAUDRATE 250000
#define ENABLE_POWER_ON_STARTUP
#define POWER_INVERTING false
#define KILL_METHOD 1
#define GCODE_BUFFER_SIZE 2
#define ACK_WITH_LINENUMBER
#define WAITING_IDENTIFIER "wait"
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

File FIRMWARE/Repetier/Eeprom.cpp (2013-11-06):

/*
    This file is part of Repetier-Firmware.

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
    This firmware is a nearly complete rewrite of the sprinter firmware
    by kliment (https://github.com/kliment/Sprinter)
    which based on Tonokip RepRap firmware rewrite based off of Hydra-mmm firmware.

  Functions in this file are used to communicate using ascii or repetier protocol.
*/

#include "Reptier.h"

#if EEPROM_MODE!=0
#include "Eeprom.h"
extern void epr_eeprom_to_data();

byte epr_compute_checksum() {
  int i;
  byte checksum=0;
  for(i=0;i<2048;i++) {
    if(i==EEPROM_OFFSET+EPR_INTEGRITY_BYTE) continue;
    checksum += eeprom_read_byte ((unsigned char *)(i));
  }
  return checksum;
}



inline void epr_set_byte(uint pos,byte value) {
  eeprom_write_byte((unsigned char *)(EEPROM_OFFSET+pos), value);
}
inline void epr_set_int(uint pos,int value) {
  eeprom_write_word((unsigned int*)(EEPROM_OFFSET+pos),value);
}
inline void epr_set_long(uint pos,long value) {
  eeprom_write_dword((unsigned long*)(EEPROM_OFFSET+pos),value);
}
inline void epr_set_float(uint pos,float value) {
  eeprom_write_block(&value,(void*)(EEPROM_OFFSET+pos), 4);
}
void epr_out_prefix(uint pos) {
  if(pos<EEPROM_EXTRUDER_OFFSET) return;
  int n = (pos-EEPROM_EXTRUDER_OFFSET)/EEPROM_EXTRUDER_LENGTH+1;
  OUT_P_I("Extr.",n);
  out.print(' ');
}
void epr_out_float(uint pos,PGM_P text) {
  OUT_P("EPR:3 ");
  OUT(pos);
  OUT(' ');
  OUT(epr_get_float(pos));
  OUT(' ');
  epr_out_prefix(pos);
  out.println_P(text);  
}
void epr_out_long(uint pos,PGM_P text) {
  OUT_P("EPR:2 ");
  OUT(pos);
  OUT(' ');
  OUT(epr_get_long(pos));
  OUT(' ');
  epr_out_prefix(pos);
  out.println_P(text);  
}
void epr_out_int(uint pos,PGM_P text) {
  OUT_P("EPR:1 ");
  OUT(pos);
  OUT(' ');
  OUT(epr_get_int(pos));
  OUT(' ');
  epr_out_prefix(pos);
  out.println_P(text);  
}
void epr_out_byte(uint pos,PGM_P text) {
  OUT_P("EPR:0 ");
  OUT(pos);
  OUT(' ');
  OUT((int)epr_get_byte(pos));
  OUT(' ');
  epr_out_prefix(pos);
  out.println_P(text);  
}

void epr_update(GCode *com) {
  if(GCODE_HAS_T(com) && GCODE_HAS_P(com)) switch(com->T) {
    case 0:
      if(GCODE_HAS_S(com)) epr_set_byte(com->P,(byte)com->S);
      break;
    case 1:
      if(GCODE_HAS_S(com)) epr_set_int(com->P,(int)com->S);
      break;
    case 2:
      if(GCODE_HAS_S(com)) epr_set_long(com->P,(long)com->S);
      break;
    case 3:
      if(GCODE_HAS_X(com)) epr_set_float(com->P,com->X);
      break;
  }
  byte newcheck = epr_compute_checksum();
  if(newcheck!=epr_get_byte(EPR_INTEGRITY_BYTE))
    epr_set_byte(EPR_INTEGRITY_BYTE,newcheck);
  epr_eeprom_to_data();
}

/** \brief Copy data from EEPROM to variables.
*/
void epr_eeprom_reset() {
  byte version = EEPROM_PROTOCOL_VERSION;
  baudrate = BAUDRATE;
  max_inactive_time = MAX_INACTIVE_TIME*1000L;
  stepper_inactive_time = STEPPER_INACTIVE_TIME*1000L;
  axis_steps_per_unit[0] = XAXIS_STEPS_PER_MM;
  axis_steps_per_unit[1] = YAXIS_STEPS_PER_MM; 
  axis_steps_per_unit[2] = ZAXIS_STEPS_PER_MM;
  axis_steps_per_unit[3] = 1;
  max_feedrate[0] = MAX_FEEDRATE_X;
  max_feedrate[1] = MAX_FEEDRATE_Y;
  max_feedrate[2] = MAX_FEEDRATE_Z;
  homing_feedrate[0] = HOMING_FEEDRATE_X;
  homing_feedrate[1] = HOMING_FEEDRATE_Y;
  homing_feedrate[2] = HOMING_FEEDRATE_Z;
  printer_state.maxJerk = MAX_JERK;
  printer_state.maxZJerk = MAX_ZJERK;
#ifdef RAMP_ACCELERATION
  max_acceleration_units_per_sq_second[0] = MAX_ACCELERATION_UNITS_PER_SQ_SECOND_X;
  max_acceleration_units_per_sq_second[1] = MAX_ACCELERATION_UNITS_PER_SQ_SECOND_Y;
  max_acceleration_units_per_sq_second[2] = MAX_ACCELERATION_UNITS_PER_SQ_SECOND_Z;
  max_travel_acceleration_units_per_sq_second[0] = MAX_TRAVEL_ACCELERATION_UNITS_PER_SQ_SECOND_X;
  max_travel_acceleration_units_per_sq_second[1] = MAX_TRAVEL_ACCELERATION_UNITS_PER_SQ_SECOND_Y;
  max_travel_acceleration_units_per_sq_second[2] = MAX_TRAVEL_ACCELERATION_UNITS_PER_SQ_SECOND_Z;
#endif
#if USE_OPS==1
  printer_state.opsMode = OPS_MODE;
  printer_state.opsMinDistance = OPS_MIN_DISTANCE;
  printer_state.opsRetractDistance = OPS_RETRACT_DISTANCE;
  printer_state.opsRetractBacklash = OPS_RETRACT_BACKLASH;
  printer_state.opsMoveAfter = OPS_MOVE_AFTER;
#endif
#if HAVE_HEATED_BED
  heatedBedController.heatManager= HEATED_BED_HEAT_MANAGER;
#ifdef TEMP_PID
  heatedBedController.pidDriveMax = HEATED_BED_PID_INTEGRAL_DRIVE_MAX;
  heatedBedController.pidDriveMin = HEATED_BED_PID_INTEGRAL_DRIVE_MIN;
  heatedBedController.pidPGain = HEATED_BED_PID_PGAIN;
  heatedBedController.pidIGain = HEATED_BED_PID_IGAIN;
  heatedBedController.pidDGain = HEATED_BED_PID_DGAIN;
  heatedBedController.pidMax = HEATED_BED_PID_MAX;
#endif
#endif
  printer_state.xLength = X_MAX_LENGTH;
  printer_state.yLength = Y_MAX_LENGTH;
  printer_state.zLength = Z_MAX_LENGTH;
  printer_state.xMin = X_MIN_POS;
  printer_state.yMin = Y_MIN_POS;
  printer_state.zMin = Z_MIN_POS;
#if ENABLE_BACKLASH_COMPENSATION
  printer_state.backlashX = X_BACKLASH;
  printer_state.backlashY = Y_BACKLASH;
  printer_state.backlashZ = Z_BACKLASH;
#endif
  Extruder *e;
#if NUM_EXTRUDER>0
  e = &extruder[0];
  e->stepsPerMM = EXT0_STEPS_PER_MM;
  e->maxFeedrate = EXT0_MAX_FEEDRATE;
  e->maxStartFeedrate = EXT0_MAX_START_FEEDRATE;
  e->maxAcceleration = EXT0_MAX_ACCELERATION;
  e->tempControl.heatManager = EXT0_HEAT_MANAGER;
#ifdef TEMP_PID
  e->tempControl.pidDriveMax = EXT0_PID_INTEGRAL_DRIVE_MAX;
  e->tempControl.pidDriveMin = EXT0_PID_INTEGRAL_DRIVE_MIN;
  e->tempControl.pidPGain = EXT0_PID_P;
  e->tempControl.pidIGain = EXT0_PID_I;
  e->tempControl.pidDGain = EXT0_PID_D;
  e->tempControl.pidMax = EXT0_PID_MAX;
#endif
  e->yOffset = EXT0_Y_OFFSET;
  e->xOffset = EXT0_X_OFFSET;
  e->watchPeriod = EXT0_WATCHPERIOD;
#if RETRACT_DURING_HEATUP
  e->waitRetractTemperature = EXT0_WAIT_RETRACT_TEMP;
  e->waitRetractUnits = EXT0_WAIT_RETRACT_UNITS;
#endif
  e->coolerSpeed = EXT0_EXTRUDER_COOLER_SPEED;
#ifdef USE_ADVANCE
#ifdef ENABLE_QUADRATIC_ADVANCE
  e->advanceK = EXT0_ADVANCE_K;
#endif
  e->advanceL = EXT0_ADVANCE_L;
#endif
#endif // NUM_EXTRUDER>0
#if NUM_EXTRUDER>1
  e = &extruder[1];
  e->stepsPerMM = EXT1_STEPS_PER_MM;
  e->maxFeedrate = EXT1_MAX_FEEDRATE;
  e->maxStartFeedrate = EXT1_MAX_START_FEEDRATE;
  e->maxAcceleration = EXT1_MAX_ACCELERATION;
  e->tempControl.heatManager = EXT1_HEAT_MANAGER;
#ifdef TEMP_PID
  e->tempControl.pidDriveMax = EXT1_PID_INTEGRAL_DRIVE_MAX;
  e->tempControl.pidDriveMin = EXT1_PID_INTEGRAL_DRIVE_MIN;
  e->tempControl.pidPGain = EXT1_PID_P;
  e->tempControl.pidIGain = EXT1_PID_I;
  e->tempControl.pidDGain = EXT1_PID_D;
  e->tempControl.pidMax = EXT1_PID_MAX;
#endif
  e->yOffset = EXT1_Y_OFFSET;
  e->xOffset = EXT1_X_OFFSET;
  e->watchPeriod = EXT1_WATCHPERIOD;
#if RETRACT_DURING_HEATUP
  e->waitRetractTemperature = EXT1_WAIT_RETRACT_TEMP;
  e->waitRetractUnits = EXT1_WAIT_RETRACT_UNITS;
#endif
  e->coolerSpeed = EXT1_EXTRUDER_COOLER_SPEED;
#ifdef USE_ADVANCE
#ifdef ENABLE_QUADRATIC_ADVANCE
  e->advanceK = EXT1_ADVANCE_K;
#endif
  e->advanceL = EXT1_ADVANCE_L;
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

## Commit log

2013-05-28 Updating cad/assy folders
2013-05-28 Adding source CAD Files etc...
    [SHEET1.DXF, SHEET2.DXF, SHEET4.DXF]
2013-05-28 added stl and iges files
    [0250-20 T-slot Nut.IGS, 0250-20 x 0500L Button Head Cap Screw.IGS, 10-32 x 0625L Pan Head Screw Natural Nylon.IGS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]
2013-05-28 added belt clamp stl
    [71622 Belt Clamp.stl]
2013-05-29 added PDF of melamine parts BOM
2013-05-30 Added a couple of new Figures and made a number of suggested revisions.
2013-05-30 Refreshed PDF to match current draft.
2013-05-31 Added Software & configuration sections and started on the calibration section.
2013-06-02 Finished off calibration section.
2013-06-04 Fixed error in e-step count for Steve's Extruder users. I had inadvertantly used the figure for RAMBo 1.0 (1/8th step) boards instead of 1.1 (1/16th step) boards.
2013-06-14 Completed the "Your First Print" chapter!
2013-06-17 Added folder for Printable Addons
    Added folder for printable addons and upgrades for Rostock MAX
    [70766 25mm fan shroud.STL, S3_Beta_Fanshroud.stl]
2013-06-26 Added a readme and updated cad files
    Added the new sheet layouts with the EZ struder EZMOUNT files etc...
    [WOOD RMAX EZ SHEET 1 OF 3.DXF, WOOD RMAX EZ SHEET 2 OF 3.DXF, WOOD RMAX EZ SHEET 3 OF 3.DXF]
2013-06-26 Added extruder-only DXF sheet
    [RMAX EXTRUDER MOUNTING KIT.dxf]
2013-06-28 Added part numbers for top mounted extruder
    [Melamine BOM.ods]
2013-07-01 Fixed corrupted assembly guide PDF.
2013-07-04 First pass at top mounted extruder instructions.
    [Melamine BOM.ods]
2013-07-12 More tweaks to top-mounted extruder instructions.
2013-07-18 Added a missed fastener description for the top extruder mounting assembly.
2013-07-19 Added "wire guide post mounting.clip.stl" - two of these are used to mount 3/8" dowel to a tower extrusion.
    [wire guide post mounting clip.stl]
2013-07-20 Added a few corrections, most notably one where I'd accidentally inverted the effects of increasing or decreasing PRINTER_RADIUS. Thankfully, a fellow on the #seemecnc IRC channel spotted it. Nobody 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
2013-08-01 Revised Fig. 2-8 to show current wiring pattern (GRBY) and updated the text to let builders know that the currently shipping kits have the stepper motor connectors pre-wired. Misc. other text changes.
2013-08-02 Added notes about disabling the EEPROM when performing the PRINTER_RADIUS calibration step.
2013-08-13 Added hardware BOM spreadsheet.
    [Hardware BOM.ods]
2013-08-15 Added new hardware bills of material, re-organized chapter 11 and split it into two parts (A and B) to help differentiate the two different types of extruder mounts that have been shipped with the ki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
    Changed wording of how the end-stop screws were installed in order to make
    the use of the #6-32 tap the first choice.
    [Hardware BOM - Other Parts.ods, Hardware BOM - Parts Bag 1.ods, Hardware BOM - Parts Bag 2.ods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]
2013-08-19 EZProbe Experimental
    An experimental attachment for probing z height on the Rostock MAX.
    [70721 EZProbe.DXF, 70722 Probe Mount.DXF, 70723 Probe Guide.DXF]
2013-08-21 Fixed the part bag tables to give the description the correct width. Thanks to Carl Little for catching this one for me.
    [Hardware BOM - Parts Bag 1.ods, Hardware BOM - Parts Bag 2.ods, Hardware BOM - Parts Bag 3.ods]
2013-08-22 Extended version of the probe guide.
    [70723 Probe Guide extended.dxf]
2013-09-03 Fixed an error with the screw length specfied for the Cheapskate Axles. I'd originally specified 1.75" and it should have been 2".
2013-09-06 A few error corrections and added a 40W soldering iron to the required materials list.
2013-09-09 Changed size of RAMBo mounting screws.
2013-10-02 Added new information covering the new delta arms and the new nozzle design.
2013-11-06 Added Firmware Folder for Rostock MAX
    Added Folder for Repetier Firmware used on the Rostock MAX kits from the
    shop
    [Configuration.h]
2013-11-08 Clarified some wiring & extruder mount points
2013-11-11 New calibration graphic
2013-11-16 Updated with a new appendix and a delta radius calibration chart.
2014-02-12 Added Appendix C to cover revised calibration instructions for the 0.91 firmware update.
2014-02-16 Corrected Fig. C-2 and added an additional warning about routing stepper wires along side end-stop wires.
2014-05-23 Added DXF files to /CAD
    Added the DXF files for the early side mounted extruder hanger -to-
    EZstruder adapter parts
    [EZSTRUDER_HANGER_ADAPTER.DXF]

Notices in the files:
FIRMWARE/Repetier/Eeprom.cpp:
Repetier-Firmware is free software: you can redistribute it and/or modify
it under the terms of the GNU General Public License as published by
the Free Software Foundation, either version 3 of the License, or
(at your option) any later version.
